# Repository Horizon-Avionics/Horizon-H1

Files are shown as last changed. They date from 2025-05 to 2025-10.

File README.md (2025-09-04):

# Horizon Avionics

## Building a fully open-source flight computer.

### Hardware By @Scooter Y, and @Meddy B.
### Software By: @Stars, and @Chocowafer

------

#### About:

The Goal of Horizon Avionics is to be able to build a full-fledged, and open-source flight computer for amateur rocketry. There is no such board online, and we are hoping for this board to streamline open-sourcing products instead of charging upwards of $400 for a ~$130 board.

#### Features:

- This whole board including antennas are under $150 USD.

- IMU/Baro for our sensor data.

- GPS for navigation of where the rocket landed and it's flight path.

- RF - Including a transmit tower for receiving/sending data from the rocket live during the flight.

- NAND + Micro SD Card Storage for logging.

- 3 MCU's each controlling different ascpetcs of the flight computer- MMCU, TMCU, NMCU.

- H-Bridge for servo movement.

- Working PWM for TVC and/or Reaction Wheel

- Pyro-channels for parachute deployment

  ------

#### How it's all gonna work:

For the most part, this will all be explained over on the software repo, but a short synopsis will be provided below.

In short, we have 3 micro-controllers, the MMCU, the TMCU, and the NMCU. Each one of these MCU's is responsible for a different aspect of the functionality of the flight computer.  

- **The TMCU**

	The TMCU is responsible for a number of different things. It takes in all the raw data from the IMU, Baro and the GPS data and sending it to the MMCU via SPI for filtering and logging. It is also resposible for sending and receiving the radio packets. In-short, the TMCU does a lot of different things for this board to make room for the MMCU to do the heavy lifting.

- **The NMCU**

  The NMCU is responsible for more of the physical actions of the rocket. It's main jobs are to on boot, load the saved state, for position movements, and while in-flight, it's jobs are to take in the filtered data from the MMCU, and use it to control the Camera, servo lines, reaction wheel, and pyro-channels.

- **The MMCU**

  The MMCU is our main MCU. It's main responsibilities are to, while in flight, take in all the data from the TMCU, put it through a filter (we will be using the Kalman Filter for our board as it is the best one we have found to remove noise and such), package the data, and send it back off to the TMCU for radio sending or to the NMCU for movments. Along with sending it to the nessecary MCU's, it also sends the packaged, and filtered data to the NAND which will eventually be moved to the SD Card + the Camera footage upon landing.

------

#### Getting Started

To view the different changes between commits, check it out over on [CADLAB.io](https://cadlab.io/project/29344).

##### Checkout locally

1. `git clone https://github.com/Horizon-Avionics/Horizon-Avionics-Hardware`

2. Open the corresponding folder in KiCad 9.0

### Some Photos So Far







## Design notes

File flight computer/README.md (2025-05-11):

# Horizon Avionics

## Building a fully open-source flight computer. Built by Hack Clubbers For Hack Clubbers

### By @Scooter Y, @Stars, @Meddy B, @YourLocalDndNerd

------

#### About:

The Goal of Horizon Avionics was to be able to build a full-fledged, and open-source flight computer for amateur rocketry. There is no such board online, and we are hoping for this board to streamline open-sourcing products instead of charging upwards of $400 for a ~$100 board.

#### Goals:

- Keep this board under $150 USD

- IMU/Baro

- GPS

- RF - Including a transmit tower for receiving/sending data from the rocket

- NAND + Micro SD Card Storage for logging

- 3 MCU's - MMCU, TMCU, NMCU

- H-Bridge

- Working PWM for TVC and/or Reaction Wheel

  ------

#### How it's all gonna work:

For the most part, this will all be explained over on the software repo, but a short synopsis will be provided below.

In short, we have 3 micro-controllers, the MMCU, the TMCU, and the NMCU. Each one of these MCU's is responsible for a different aspect of the functionality of the flight computer.  

- **The TMCU**

	The TMCU is responsible for a number of different things. It takes in all the raw data from the IMU, Baro and the GPS data and sending it to the MMCU via SPI for filtering and logging. 

- **The NMCU**

- **The MMCU**

------

#### Getting Started

To view the diff changes between commits, check it out over on [CADLAB.io](https://cadlab.io/project/29344).

##### Checkout locally

1. `git clone https://github.com/Horizon-Avionics/Horizon-Avionics-Hardware`

2. Open the corresponding folder in KiCad 9.0

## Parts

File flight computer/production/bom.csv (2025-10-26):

Designator | Footprint | Quantity | Value | LCSC Part #
1X3SERVO1 | PinHeader_1x03_P2.54mm_Vertical | 1 | Conn_01x03
BZ2 | MLT-8530_JHE | 1 | Buzzer
C1, C2 | 0603 | 2 | 100 nF
C10, C17 | 0603 | 2 | 12pF
C11, C13, C15, C19, C44, C45, C5, C50, C51, C6, C7, C77, C8, C9 | 0603 | 14 | 100nF
C12, C22, C35, C63, C72 | 0603 | 5 | 1uF
C16 | 0603 | 1 | 4n7
C18, C67 | 0603 | 2 | 4.7uF
C20, C23, R1 | 0603 | 3 | DNP
C21, C24, C25, C28, C32 | 0603 | 5 | 10uF
C26 | 0603 | 1 | 100pF
C27 | 0603 | 1 | 100n
C33 | 0603 | 1 | 3.3 nF
C34 | 0603 | 1 | 22uF
C36 | 0603 | 1 | 1u
C37, C38 | 0603 | 2 | 100nF | C14663
C4 | 0603 | 1 | 1.2 pF
C40 | 0603 | 1 | 470nF | C1623
C46 | 0603 | 1 | 1nF | C100040
C47 | 0603 | 1 | 47nF | C107093
C48 | 0603 | 1 | 47pF | C105622
C49 | 0603 | 1 | 100pF | C14665
C64, C65, C66 | 0603 | 3 | 0.1uF
D1 | 0603 | 1 | D_Schottky
D15, D16, D17, D18 | LED_ROHM_SMLVN6 | 4 | SMLVN6RGB
D20, D26 | Nexperia_CFP3_SOD-123W | 2 | PMEG6020ER
D21, D22, D3, D4, D7 | 0603 | 5 | LED
D8 | SOT-143 | 1 | PRTR5V0U2X
F1, F2 | 0603 | 2 | Polyfuse
FB1 | 0603 | 1 | BLM18AG601SN1D
J1 | microSD_HC_Hirose_DM3D-SF | 1 | Micro_SD_Card_Det1
J10 | TerminalBlock_Phoenix_MPT-0,5-2-2.54_1x02_P2.54mm_Horizontal | 1 | Conn_01x02_Pin
J11 | USB_C_Receptacle_GCT_USB4105-xx-A_16P_TopMnt_Horizontal | 1 | USB_C_Receptacle_USB2.0_16P
J12 | PinHeader_1x04_P2.54mm_Vertical | 1 | Conn_01x04
J13, J14, J6, J9 | PinHeader_1x03_P2.54mm_Vertical | 4 | 1x3 servo
J15, J16 | TerminalBlock_Phoenix_MPT-0,5-2-2.54_1x02_P2.54mm_Horizontal | 2 | arming terminal
J17, J3, J4 | U.FL_Hirose_U.FL-R-SMT-1_Vertical | 3 | H9161TR-ND
J18, J2, J21, J7, J8 | PinHeader_2x03_P2.54mm_Vertical | 5 | Conn_02x03_Counter_Clockwise
J19, J20 | TerminalBlock_Phoenix_MPT-0,5-2-2.54_1x02_P2.54mm_Horizontal | 2 | Screw_Terminal_01x02
J22 | PinHeader_2x03_P2.54mm_Vertical | 1 | Bluetooth Programming
J5 | TerminalBlock_Phoenix_MPT-0,5-2-2.54_1x02_P2.54mm_Horizontal | 1 | Screw_Term
L10 | 0603 | 1 | 47nH | C285885
L11 | 0805 | 1 | 15uH | C383402
L2 | L_APV_ANR4018 | 1 | 2.2uH
L3 | 0603 | 1 | 3.9 nH
Q2 | SOT-23 | 1 | DMG2301L
Q7 | SOT-23 | 1 | BSS138
Q8, Q9 | SOT-23 | 2 | IRLML6402
R10, R13, R26, R29, R30 | 0603 | 5 | 2.2k
R11, R12, R54, R55 | 0603 | 4 | 10kΩ
R14, R9 | 0603 | 2 | 1.5k
R2 | 0603 | 1 | 0R
R20, R21 | 0603 | 2 | 5k1
R22, R47 | 0603 | 2 | 330
R27, R3, R38, R39, R4, R5, R52, R53, R56, R78, R80 | 0603 | 11 | 10k
R42 | 1206 | 1 | 900k
R43, R45 | 0603 | 2 | 100k
R44 | 0603 | 1 | 350k
R46, R79, R81 | 0603 | 3 | 100
R58, R59 | 0603 | 2 | 1k
R6, R7 | 0603 | 2 | 4.7k
R72 | 0603 | 1 | 2k2
R8 | 0603 | 1 | 100 | C105588
R87, R88, R89, R90, R91, R92, R93, R94, R95, R96, R97, R98 | 0603 | 12 | 220
SAMD21G18A-AU1 | TQFP-48_7x7mm_P0.5mm | 1 | NMCU
SAMD21G18A-AU2 | TQFP-48_7x7mm_P0.5mm | 1 | TMCU
SW1 | SW_SPST_CK_KMS2xxGP | 1 | CK_KMS2xxG
U1 | QFP50P1200X1200X160-64N | 1 | MMCU
U10 | LGA-14_3x2.5mm_P0.5mm_LayoutBorder3x4y | 1 | LSM6DS3
U11 | BGM220S_SIL | 1 | BGM220SC12WGA2R
U13 | TSOT-23-6 | 1 | LTC4412xS6
U15 | SOT-23-5 | 1 | AP2112K-3.3
U16 | QFN-24-1EP_4x4mm_P0.5mm_EP2.6x2.6mm | 1 | SX1262IMLTRT | C191341
U17 | SOT-363_SC-70-6 | 1 | PE4259 | C470892
U2 | QFN-16-1EP_3x3mm_P0.5mm_EP1.9x1.9mm | 1 | MKL02Z32VFG4
U3 | Texas_S-PVSON-N10_ThermalVias | 1 | TPS61200DRC
U5 | ST_HLGA-10_2x2mm_P0.5mm_LayoutBorder3x2y | 1 | LPS22HB
U6 | Quectel_L96 | 1 | GPS
U8 | SOIC-8_5.3x5.3mm_P1.27mm | 1 | NAND
U9 | Texas_SIL0008D_MicroSiP-8-1EP_2.8x3mm_P0.65mm_EP1.1x1.9mm_ThermalVias | 1 | TPS82130
Y1 | Crystal_SMD_3215-2Pin_3.2x1.5mm | 1 | 32 kHZ
Y2 | Crystal_SMD_3225-4Pin_3.2x2.5mm | 1 | 32MHz | C37635386

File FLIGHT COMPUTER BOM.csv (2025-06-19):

Manufacturer Part Number | Quantity | Digi-Key Part Number | Total Price | Customer Reference
MK20DX256VLH7 | 1 | MK20DX256VLH7-ND | $11.94
W25Q128JVSIQ | 1 | W25Q128JVSIQ-ND | $2.39
A3909GLNTR-T | 1 | 620-1498-1-ND | $1.92
BGM220SC12WGA2R | 1 | 336-BGM220SC12WGA2RCT-ND | $10.37
TPS61092RSAR | 1 | 296-15240-1-ND | $3.46
LTC4412IS6#TRMPBF | 1 | 505-LTC4412IS6#TRMPBFCT-ND | $9.78
TB006-508-02BE | 5 | 102-6191-ND | $3.80
61301011121 | 5 | 732-2670-ND | $6.25
AP2112K-3.3TRG1 | 1 | AP2112K-3.3TRG1DICT-ND | $0.34
PRTR5V0U2X,215 | 3 | 1727-3884-1-ND | $2.04
AT-0927-TT-6-R | 1 | 668-1462-ND | $1.53
BSS138 | 1 | BSS138CT-ND | $0.41
DM3D-SF | 1 | HR1941CT-ND | $2.46
SMLVN6RGB1W1 | 3 | 846-1187-1-ND | $6.69
ABS07-32.768KHZ-7-T | 2 | 535-9543-1-ND | $2.54
W1030 | 2 | 553-1309-ND | $11.60
1052620001 | 1 | WM9669-ND | $3.07
LG Q396-PS-35-0-20-R18 | 10 | 475-LGQ396-PS-35CT-ND | $1.86
PMEG6020ER,115 | 5 | 1727-5217-1-ND | $2.85 | D19, D20, D23, D26
0603L010YR | 3 | F2900CT-ND | $4.44
GRM022R60J104ME15L | 10 | 490-7192-1-ND | $0.36
CRGCQ0603J220R | 10 | A130087CT-ND | $0.36
RC0603FR-074K7L | 2 | 311-4.70KHRCT-ND | $0.32
RC0603FR-07430KL | 1 | 311-430KHRCT-ND | $0.16
RC0603FR-07100KL | 20 | 311-100KHRCT-ND | $0.28
RC0603FR-075K1L | 10 | 311-5.10KHRCT-ND | $0.14
RMCF0603JT10K0 | 50 | RMCF0603JT10K0CT-ND | $0.82
RC0201FR-0733RL | 10 | 311-33.0MCT-ND | $0.17
RC0201FR-071KL | 10 | 311-1KMCT-ND | $0.14
RC0603FR-072K2L | 2 | 311-2.20KHRCT-ND | $0.32
IRLML6402TRPBF | 10 | IRLML6402PBFCT-ND | $3.26
DMG2301L-7 | 1 | DMG2301L-7DICT-ND | $0.36
PPTC032LFBN-RC | 3 | S7071-ND | $2.10
61300411821 | 1 | 732-61300411821-ND | $0.58
NSR01L30MXT5G | 1 | NSR01L30MXT5GOSCT-ND | $0.26 | D1
TMK107ABJ225KA-T | 1 | 587-2909-1-ND | $0.12
CL10A226MP8NUNE | 1 | 1276-1274-1-ND | $0.12
CL10B105KP8NNNC | 10 | 1276-1946-1-ND | $0.07
GRM0335C1H1R2CA01D | 2 | 490-6119-1-ND | $0.30
C0603C332K4REC7411 | 1 | 399-C0603C332K4REC7411CT-ND | $0.15
C0603C220J5GACTU | 2 | 399-C0603C220J5GACTUCT-ND | $0.34
CL10A106KQ8NNNC | 3 | 1276-1038-1-ND | $0.36
C0603C103M4REC7411 | 10 | 399-C0603C103M4REC7411CT-ND | $0.79
C0603X102K5RAC3316 | 2 | 399-C0603X102K5RAC3316CT-ND | $1.02
CL10A475KP8NNNC | 2 | 1276-1044-1-ND | $0.24
C0603C472K4RECAUTO | 3 | 399-17879-1-ND | $0.57
CBR02C120F3GAC | 2 | 399-8604-1-ND | $1.10
B82496C3470J000 | 1 | 495-1838-1-ND | $0.41
LRC0201BS3N9GV001T | 2 | 712-LRC0201BS3N9GV001TCT-ND | $0.30
RC0603FR-13330KL | 2 | 13-RC0603FR-13330KLCT-ND | $0.32 | 330 instead of 350K
PESD5V0S1UL,315 | 1 | 1727-4189-1-ND | $0.19 | D2
CONMHF1-SMD-T | 1 | 343-CONMHF1-SMD-TCT-ND | $0.29
124019772112A | 1 | 664-124019772112ACT-ND | $2.73
0733910070 | 2 | WM5544-ND | $10.94
ATSAMD21G18A-AU | 2 | ATSAMD21G18A-AU-ND | $12.90
CC0603KRX5R8BB104 | 38 | 13-CC0603KRX5R8BB104CT-ND | $1.94
GRM0335C1H2R7CA01D | 2 | 490-11323-1-ND | $0.30
GRM0335C1H2R2CA01D | 10 | 490-6125-1-ND | $0.20
C0603X104M5RACTU | 1 | 399-C0603X104M5RACTUCT-ND | $0.60
GRM0335C1H1R8CA01D | 2 | 490-11314-1-ND | $0.30
GJM0335C1E1R0WB01D | 2 | 490-10677-1-ND | $0.32
GJM0335C1E1R5BB01D | 2 | 490-11175-1-ND | $0.30
XL2ED8K5OI-111YXC-32M | 2 | 4029-XL2ED8K5OI-111YXC-32MCT-ND | $1.00
0734120114 | 1 | WM3894CT-ND | $1.28
LQM18DN6R8M70L | 1 | 490-LQM18DN6R8M70LCT-ND | $0.17
LSM6DSO32TR | 1 | 497-LSM6DSO32CT-ND | $5.66
ERJ-1GNF1000C | 10 | P122654CT-ND | $0.60
LQG18HN6N8J00D | 2 | 490-1108-1-ND | $0.40
LQP03TN8N2H02D | 2 | 490-6740-1-ND | $0.30
L96-M33 | 1 | 2958-L96-M33CT-ND | $20.64
C470892 | 3 |  | $1.86
C94049 | 3 |  | $2.30
C163210 | 3 |  | $5.25
C3013581 | 100 |  | $0.81
C90205 | 100 |  | $0.58
SW1, SW2
TP1, TP2
R26, R29, R30
TOTAL BEFORE TAX + SHIPPING |  |  | $177.44USD

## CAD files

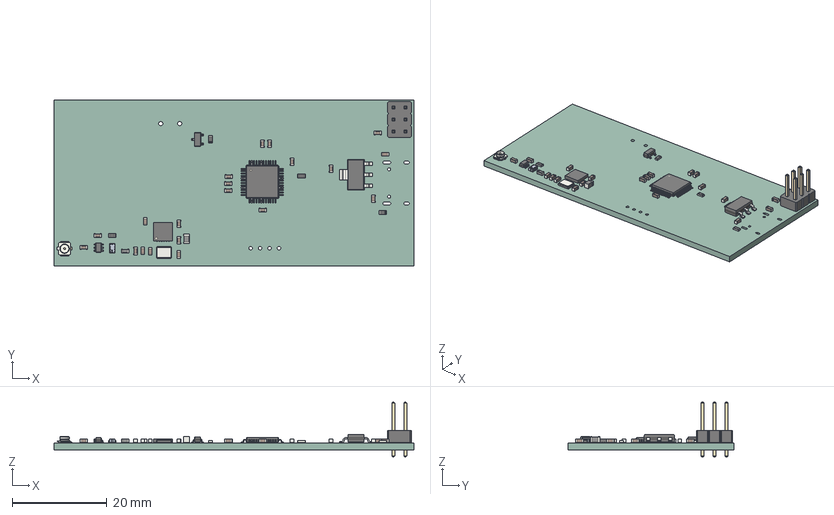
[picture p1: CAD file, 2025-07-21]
ground station/gs.step
76.0 x 35.0 x 11.5 mm
C_0603_1608Metric x 20
R_0603_1608Metric x 4
L_0603_1608Metric
SOT-23
Crystal_SMD_3225-4Pin_3.2x2.5mm
U.FL_Hirose_U.FL-R-SMT-1_Vertical
SOT-363_SC-70-6
SOT-223
QFN-24-1EP_4x4mm_P0.5mm_EP2.6x2.6mm
gs 1.27.1
gs 1.27.2
gs 1.27.3
PinHeader_2x03_P2.54mm_Vertical
TQFP-48_7x7mm_P0.5mm
L_0805_2012Metric
gs_PCB

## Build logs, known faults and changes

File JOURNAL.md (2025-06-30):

Day 1- Friday \- \~4 hours:

- Came up with the idea of building a fully open-source flight computer for amateur rocketry.  
- Started to put together a team, and started researching parts to use  
- Came up with a rough-plan on what we want out of this and our parts selection (On Tab 1 on all the charts)

Day 2- Saturday \- \~3 Hours:

- Finalized parts selections  
- Started work on software

Day 3 \- sunday \- \~7.5

- discussed potential solutions in order to program all 3 chips with 1 usb-c connector  
- looked into alternatives, and what other people have done  
- looked into additional sensors/regulators that we will use  
- Continued to work on software- developed most of the code for the IMU’s, GPS and stuff.

Day 4 \- monday \- \~4 hours:

- Figuring out a big bug in the code and  
- final solution for programming   
- working on solution for data/power, and allowing us to flash 3 MCU’s with only one USB-C connector

Day 5 \- tuesday \- \~6.5 hours (3.5 hours huddle, 2 hours Meddy by himself afterwards, and 1 hour just Liam for software):

- Finished the switch multiplexer stuff.  
- Finished the solution for data/power, and allowing us to flash 3 MCU’s with only one USB-C connector  
- Changed a few small power rail stuff

Day 6 \- Wednesday \- \~4 hours:

- Built the full schematics for the IMU via SPI to the TMCU/

Day 7 \- Thursday \- \~4.5 hours from @Scooter Y, 4 hours from @Meddy B:

- Finally finished building the GPS module  
  - Had to figure out how to wire up the antenna, and which one to use (which ended up being the LNA one…)  

- Finished wiring up the radio tuned at 915 MHZ to bypass HAM restrictions including all the SPI magic and the antennas for it  
  
- Built the schematic for the H-Bridge which is responsible for controlling the servos for the reaction wheel  

- Fixed some net flag issues where I forgot to wire it to the MCU…

Day 9- Saturday- \~8 hours from @Scooter Y, @Meddy B, and @Stars:

- Added Bluetooth to the Schematic for making changes to the codebase and flashing it to the MCU’s wirelessly (especially useful on the launch pad for last minute changes). A big   
  Trouble was trying to figure out how to get it to 2.3GHZ. I had to calc π-type to figure out what to use to get it to the right frequency.  



- 

Day 10 \- sunday the 18th \~15 hours from @meddy and @scooter y (We worked from like 1am to 4am\!)

- Today was a big day for us. We started off with doing some schematic work and adding a lot of the needed footprints like for BL. After that, we did the layout for pcb and wired up sensors and putting it on the pcb, although U didnt finish wiring everything to the power rails and mcu. I (@scooter) started the routing too for the bl chip, along with the cs, sck for rf chip as that takes time since it is a very sensitive ic. ill finish after i sleep. i need to fix the jtag/swd connectors as well.





Day 11 \- Thursday \- May 22nd \- 4 hours

- started redoing layout

Day 12 \- Friday \- May 23rd \- 13 hours

- Started wiring, got stuck and realized the layout was bad so I scrapped it and did it again so I started a new layout. We didn’t have enough space on the PCB to properly route all the sensitive components. Also, idk what we were on, but we also had WAY too many screw terminals, we should only have like 5, not 12\.

Day 13 \- saturday \- May 24th \- 2 hours

- I realized the layout was bad so I did it one more time. Started it- not finished it ;)

Day 14 \- sunday \- May 25th \- 5 hours

- redid layout, starting wiring some more, and this time, it finally seems to be a lot nicer




Through every revision it looks very similar because we have an idea of what we want with the end result, but the process of laying out every single part and the specific wiring seems to change so its not really the same every time. For example for this revision, we have the screw terminals on the top to allow more space on the sides for ant’s and stuff.

Day 15 \- May 26th \- 3 hours (@Meddy)

- Don’t really remember what I exactly wired up on this day :pf:, but I did some PCB routing, most likely regarding the MCU routing.

Day 16 \- May 27th \- 4 hours

- Did some more routing on this day- nothing crazy. I mostly re-arranged this github repo’s folders since it was a mess\!

Ive worked on it at random misc times and forgot to record  
Day 17(latest day ive acc recorded) 6/1 13 hours

- I completely redid the entire layout. Our first approach was laying everything out and then wiring, whereas with my latest version, I was focused on completing entire parts. Like completely wiring everything for a sensor, before wiring up the next part. I think this approach helped cuz now everything is actually able to fit(except the bootloader pins). The good thing is even though it was a full re-wiring, the layout was kept very similar, and it was more the way I routed it over the parts placement.  

- finished complete wiring, still need bootloader pins. worst case scenario ill will the wires directly to the mcu  



Day 18 \- June 2nd \- 5 hours:

- literally just random wiring

Day 19 \- June 3rd \- 6 hours:

- Finished the layout placement ie. all the parts are now all placed now, and just the few left need to be routed, and all the MCU routing. 

Day 20 \- June 4th \- 4 hours:

- Fixes over 200 DRC errors. Now I only have 84 errors left (yay, I guess).... I also wired up the bootloader pins which will be able to be broken off once programmed for the first time. I routed this with Meddy.

Day 21 \- June 5th: maybe 3 hours?

- finally a day without wiring. fixed all drc errors. I started working on the warnings, and then I realized that I could ignore them since they were all about the silkscreens. Instead I only needed to fix the actual errors. I did that. A lot of traces didn't have space between each other since everything is so tightly packed. I cleaned up random misc traces and stuff. Everything should pretty much be good now.

Day 22 \- June 6th: 3 hours:

- So apparently even though we thought there were no DRC errors left, there somehow were :(. For some reason each device said more so we fixed those (which were actual DRC errors, I'm confused.) Nonetheless, we fixed most of the DRC errors.

Day 23 \- June 13th: 3 hours:

- Tided everything up, and finally finished all the hole DRC’s \+ trace spacing DRC’s\!

Day 24 \- 4 hours:

- I fixed the ground pour to be all 4 layers over just the top and bottom since it would be better. I also switched out the BL, and GPS antenna’s to U.FL since apparently SMA antennas for these don’t exist.. I also did some ground stitching around the GPS, BL, and RF since those need to have ground stitching and I didn’t add it yet.

Day 25 \- June 18th \- 10 minutes:

- Added the PCBWAY logo to our board since they will be sponsoring the PCB it seems like.

All of @yourlocaldndnerd's time \- 13 hours programming + \~30 hours of docs and design
- I keep forgetting to add any of my time, so this is all of mine combined into one slot.
- I mostly just programmed the gps, radio (which were completed by around day 15), and the kalman filters (still needs testing)

**Total hours worked on it so far- \~128.6 hours**  
**Links-**   
[**https://github.com/Horizon-Avionics/Horizon-Avionics-Hardware**](https://github.com/Horizon-Avionics/Horizon-Avionics-Hardware)  
[**https://github.com/Horizon-Avionics/Horizon-Avionics-Software**](https://github.com/Horizon-Avionics/Horizon-Avionics-Software)

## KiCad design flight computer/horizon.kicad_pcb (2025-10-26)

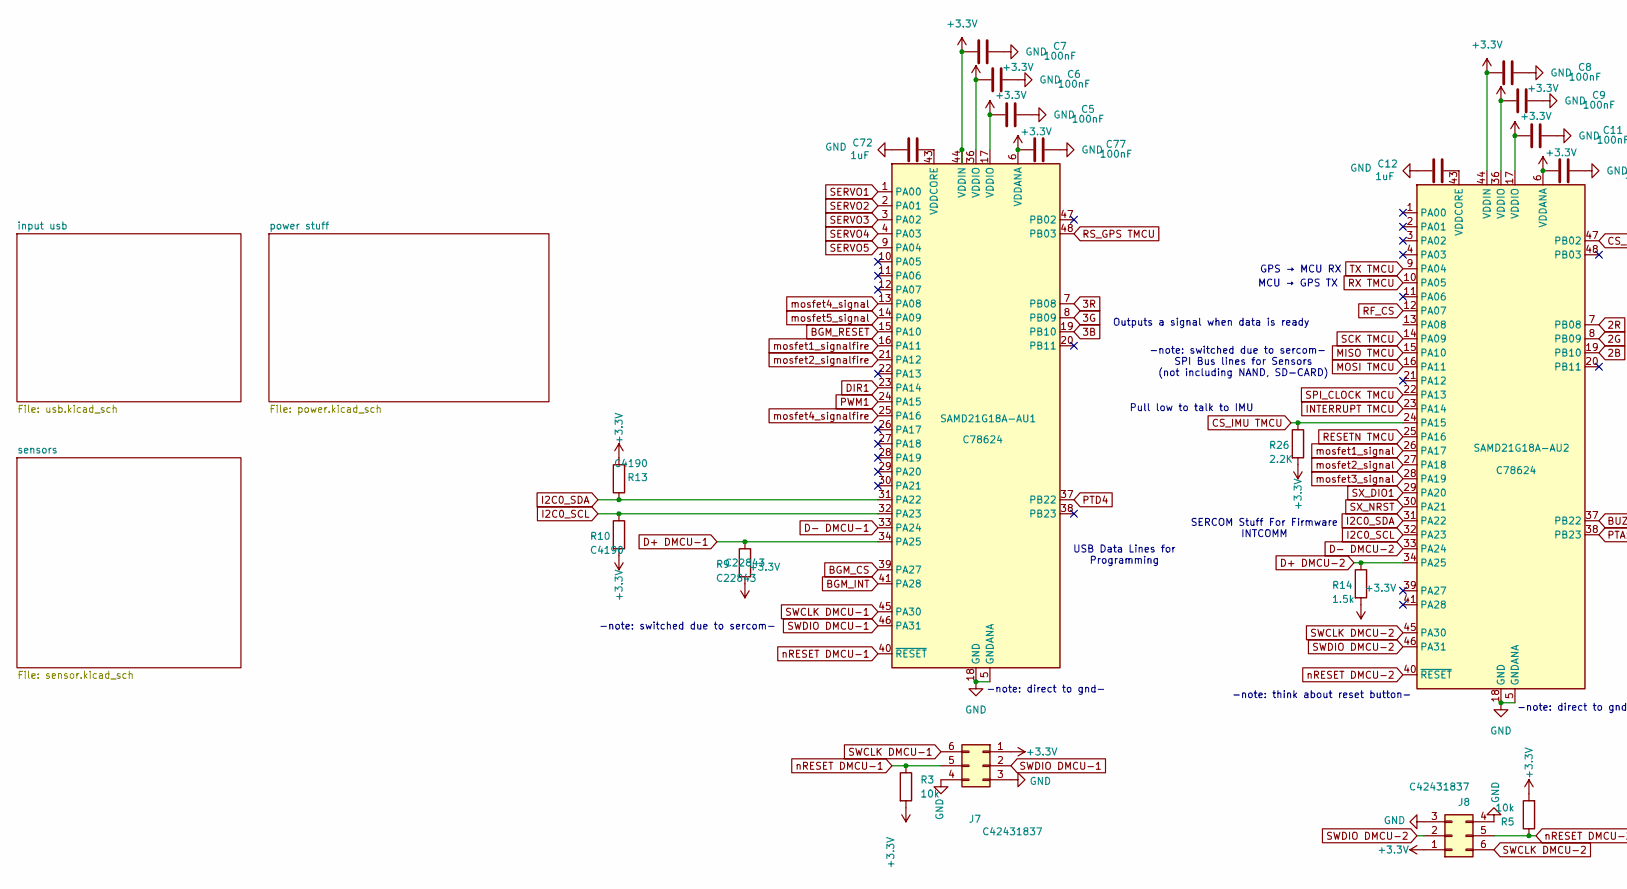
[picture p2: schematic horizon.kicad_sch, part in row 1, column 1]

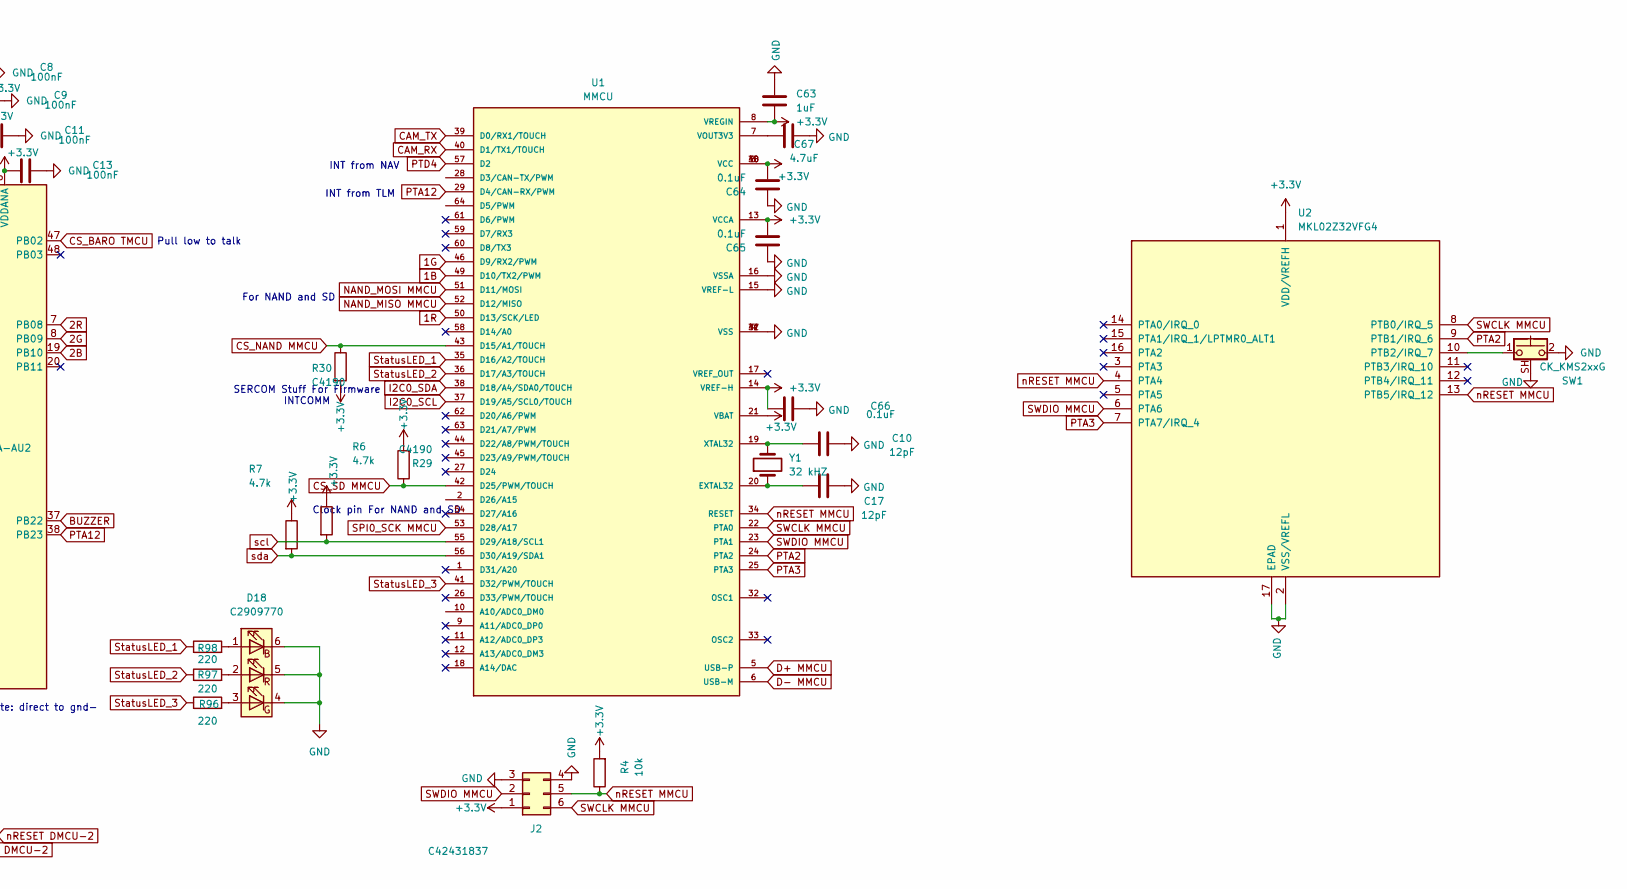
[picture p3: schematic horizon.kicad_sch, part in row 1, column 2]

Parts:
C5, C6, C7, C8, C9, C11, C13, C77: 100nF; C_0603_1608Metric
C10, C17: 12pF; C_0603_1608Metric
C12, C63, C72: 1uF; C_0603_1608Metric
C64, C65, C66: 0.1uF; C_0603_1608Metric
C67: 4.7uF; C_0603_1608Metric
D18: C2909770; LED_ROHM_SMLVN6
J2, J7, J8: C42431837; PinHeader_2x03_P2.54mm_Vertical
R3, R4, R5: 10k; R_0603_1608Metric
R6, R7: 4.7k; R_0603_1608Metric
R9: C22843; R_0603_1608Metric; LCSC C22843
R10, R13, R29, R30: C4190; R_0603_1608Metric
R14: 1.5k; R_0603_1608Metric
R26: 2.2K; R_0603_1608Metric
R96, R97, R98: 220; R_0603_1608Metric
SAMD21G18A-AU1, SAMD21G18A-AU2: C78624; TQFP-48_7x7mm_P0.5mm
SW1: CK_KMS2xxG; SW_SPST_CK_KMS2xxGP
U1: MMCU; QFP50P1200X1200X160-64N
U2: MKL02Z32VFG4; QFN-16-1EP_3x3mm_P0.5mm_EP1.9x1.9mm
Y1: 32 kHZ; Crystal_AT310_D3.0mm_L10.0mm_Vertical

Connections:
1B: U1.49 (D10/TX2/PWM); also elsewhere on the board
1G: U1.46 (D9/RX2/PWM); also elsewhere on the board
1R: U1.50 (D13/SCK/LED); also elsewhere on the board
2B: SAMD21G18A-AU2.19 (PB10); also elsewhere on the board
2G: SAMD21G18A-AU2.8 (PB09); also elsewhere on the board
2R: SAMD21G18A-AU2.7 (PB08); also elsewhere on the board
3B: SAMD21G18A-AU1.19 (PB10); also elsewhere on the board
3G: SAMD21G18A-AU1.8 (PB09); also elsewhere on the board
3R: SAMD21G18A-AU1.7 (PB08); also elsewhere on the board
+3.3V: C5.2, C6.2, C7.2, C8.2, C9.2, C11.2, C13.2, C63.1, C64.1, C65.1, C66.1, C77.2, J2.1, J7.1, J8.1, R3.2, R4.2, R5.2, R6.1, R7.1, R9.2, R10.2, R13.2, R14.2, R26.2, R29.2, R30.2, SAMD21G18A-AU1.6 (VDDANA), SAMD21G18A-AU1.17 (VDDIO), SAMD21G18A-AU1.36 (VDDIO), SAMD21G18A-AU1.44 (VDDIN), SAMD21G18A-AU2.6 (VDDANA), SAMD21G18A-AU2.17 (VDDIO), SAMD21G18A-AU2.36 (VDDIO), SAMD21G18A-AU2.44 (VDDIN), U1.3 (VCC), U1.8 (VREGIN), U1.13 (VCCA), U1.14 (VREF-H), U1.21 (VBAT), U1.30 (VCC), U1.48 (VCC), U2.1 (VDD/VREFH); also elsewhere on the board
BGM_CS: SAMD21G18A-AU1.39 (PA27); also elsewhere on the board
BGM_INT: SAMD21G18A-AU1.41 (PA28); also elsewhere on the board
BGM_RESET: SAMD21G18A-AU1.15 (PA10); also elsewhere on the board
BUZZER: SAMD21G18A-AU2.37 (PB22); also elsewhere on the board
CAM_RX: U1.40 (D1/TX1/TOUCH); also elsewhere on the board
CAM_TX: U1.39 (D0/RX1/TOUCH); also elsewhere on the board
CS_BARO TMCU: SAMD21G18A-AU2.47 (PB02); also elsewhere on the board
CS_IMU TMCU: R26.1, SAMD21G18A-AU2.24 (PA15); also elsewhere on the board
CS_NAND MMCU: R30.1, U1.43 (D15/A1/TOUCH); also elsewhere on the board
CS_SD MMCU: R29.1, U1.42 (D25/PWM/TOUCH); also elsewhere on the board
D+ DMCU-1: R9.1, SAMD21G18A-AU1.34 (PA25); also elsewhere on the board
D+ DMCU-2: R14.1, SAMD21G18A-AU2.34 (PA25); also elsewhere on the board
D+ MMCU: U1.5 (USB-P); also elsewhere on the board
D- DMCU-1: SAMD21G18A-AU1.33 (PA24); also elsewhere on the board
D- DMCU-2: SAMD21G18A-AU2.33 (PA24); also elsewhere on the board
D- MMCU: U1.6 (USB-M); also elsewhere on the board
DIR1: SAMD21G18A-AU1.23 (PA14)
GND: C5.1, C6.1, C7.1, C8.1, C9.1, C10.2, C11.1, C12.1, C13.1, C17.2, C63.2, C64.2, C65.2, C66.2, C67.2, C72.1, C77.1, D18.4 (GK), D18.5 (RK), D18.6 (BK), J2.3, J2.4, J7.3, J7.4, J8.3, J8.4, SAMD21G18A-AU1.5 (GNDANA), SAMD21G18A-AU1.18 (GND), SAMD21G18A-AU1.35 (GND), SAMD21G18A-AU1.42 (GND), SAMD21G18A-AU2.5 (GNDANA), SAMD21G18A-AU2.18 (GND), SAMD21G18A-AU2.35 (GND), SAMD21G18A-AU2.42 (GND), SW1.2, SW1.SH (B), U1.4 (VSS), U1.15 (VREF-L), U1.16 (VSSA), U1.31 (VSS), U1.47 (VSS), U2.2 (VSS/VREFL), U2.17 (EPAD); also elsewhere on the board
I2C0_SCL: R10.1, SAMD21G18A-AU1.32 (PA23), SAMD21G18A-AU2.32 (PA23), U1.37 (D19/A5/SCL0/TOUCH); also elsewhere on the board
I2C0_SDA: R13.1, SAMD21G18A-AU1.31 (PA22), SAMD21G18A-AU2.31 (PA22), U1.38 (D18/A4/SDA0/TOUCH); also elsewhere on the board
INTERRUPT TMCU: SAMD21G18A-AU2.23 (PA14); also elsewhere on the board
MISO TMCU: SAMD21G18A-AU2.15 (PA10); also elsewhere on the board
MOSI TMCU: SAMD21G18A-AU2.16 (PA11); also elsewhere on the board
NAND_MISO MMCU: U1.52 (D12/MISO); also elsewhere on the board
NAND_MOSI MMCU: U1.51 (D11/MOSI); also elsewhere on the board
unnamed: D18.1 (BA), R98.2
unnamed: D18.3 (GA), R96.2
unnamed: D18.2 (RA), R97.2
unnamed: C72.2, SAMD21G18A-AU1.43 (VDDCORE)
unnamed: C12.2, SAMD21G18A-AU2.43 (VDDCORE)
unnamed: C17.1, U1.20 (EXTAL32), Y1.1
unnamed: C67.1, U1.7 (VOUT3V3)
unnamed: C10.1, U1.19 (XTAL32), Y1.2
unnamed: SW1.1, U2.10 (PTB2/IRQ_7)
PTA2: U1.24 (PTA2), U2.9 (PTB1/IRQ_6)
PTA3: U1.25 (PTA3), U2.7 (PTA7/IRQ_4)
PTA12: SAMD21G18A-AU2.38 (PB23), U1.29 (D4/CAN-RX/PWM)
PTD4: SAMD21G18A-AU1.37 (PB22), U1.57 (D2)
PWM1: SAMD21G18A-AU1.24 (PA15)
RESETN TMCU: SAMD21G18A-AU2.25 (PA16)
RF_CS: SAMD21G18A-AU2.12 (PA07); also elsewhere on the board
RS_GPS TMCU: SAMD21G18A-AU1.48 (PB03); also elsewhere on the board
RX TMCU: SAMD21G18A-AU2.10 (PA05); also elsewhere on the board
SCK TMCU: SAMD21G18A-AU2.14 (PA09); also elsewhere on the board
SERVO1: SAMD21G18A-AU1.1 (PA00); also elsewhere on the board
SERVO2: SAMD21G18A-AU1.2 (PA01); also elsewhere on the board
SERVO3: SAMD21G18A-AU1.3 (PA02); also elsewhere on the board
SERVO4: SAMD21G18A-AU1.4 (PA03); also elsewhere on the board
SERVO5: SAMD21G18A-AU1.9 (PA04); also elsewhere on the board
SPI0_SCK MMCU: U1.53 (D28/A17); also elsewhere on the board
SPI_CLOCK TMCU: SAMD21G18A-AU2.22 (PA13); also elsewhere on the board
SWCLK DMCU-1: J7.6, SAMD21G18A-AU1.45 (PA30)
SWCLK DMCU-2: J8.6, SAMD21G18A-AU2.45 (PA30)
SWCLK MMCU: J2.6, U1.22 (PTA0), U2.8 (PTB0/IRQ_5)
SWDIO DMCU-1: J7.2, SAMD21G18A-AU1.46 (PA31)
SWDIO DMCU-2: J8.2, SAMD21G18A-AU2.46 (PA31)
SWDIO MMCU: J2.2, U1.23 (PTA1), U2.6 (PTA6)
SX_DIO1: SAMD21G18A-AU2.29 (PA20); also elsewhere on the board
SX_NRST: SAMD21G18A-AU2.30 (PA21); also elsewhere on the board
StatusLED_1: R98.1, U1.35 (D16/A2/TOUCH)
StatusLED_2: R97.1, U1.36 (D17/A3/TOUCH)
StatusLED_3: R96.1, U1.41 (D32/PWM/TOUCH)
TX TMCU: SAMD21G18A-AU2.9 (PA04); also elsewhere on the board
mosfet1_signal: SAMD21G18A-AU2.26 (PA17)
mosfet1_signalfire: SAMD21G18A-AU1.16 (PA11); also elsewhere on the board
mosfet2_signal: SAMD21G18A-AU2.27 (PA18)
mosfet2_signalfire: SAMD21G18A-AU1.21 (PA12); also elsewhere on the board
mosfet3_signal: SAMD21G18A-AU2.28 (PA19)
mosfet4_signal: SAMD21G18A-AU1.13 (PA08)
mosfet4_signalfire: SAMD21G18A-AU1.25 (PA16)
mosfet5_signal: SAMD21G18A-AU1.14 (PA09)
nRESET DMCU-1: J7.5, R3.1, SAMD21G18A-AU1.40 (~RESET)
nRESET DMCU-2: J8.5, R5.1, SAMD21G18A-AU2.40 (~RESET)
nRESET MMCU: J2.5, R4.1, U1.34 (RESET), U2.4 (PTA4), U2.13 (PTB5/IRQ_12)
scl: R6.2, U1.55 (D29/A18/SCL1)
sda: R7.2, U1.56 (D30/A19/SDA1)

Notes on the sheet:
SERCOM Stuff For Firmware INTCOMM
-note: direct to gnd-
For NAND and SD
-note: switched due to sercom-
Pull low to talk to IMU
INT from TLM
Pull low to talk
GPS → MCU RX
Clock pin For NAND and SD
MCU → GPS TX
Outputs a signal when data is ready
-note: think about reset button-
INT from NAV
USB Data Lines for Programming
SPI Bus lines for Sensors (not including NAND, SD-CARD)

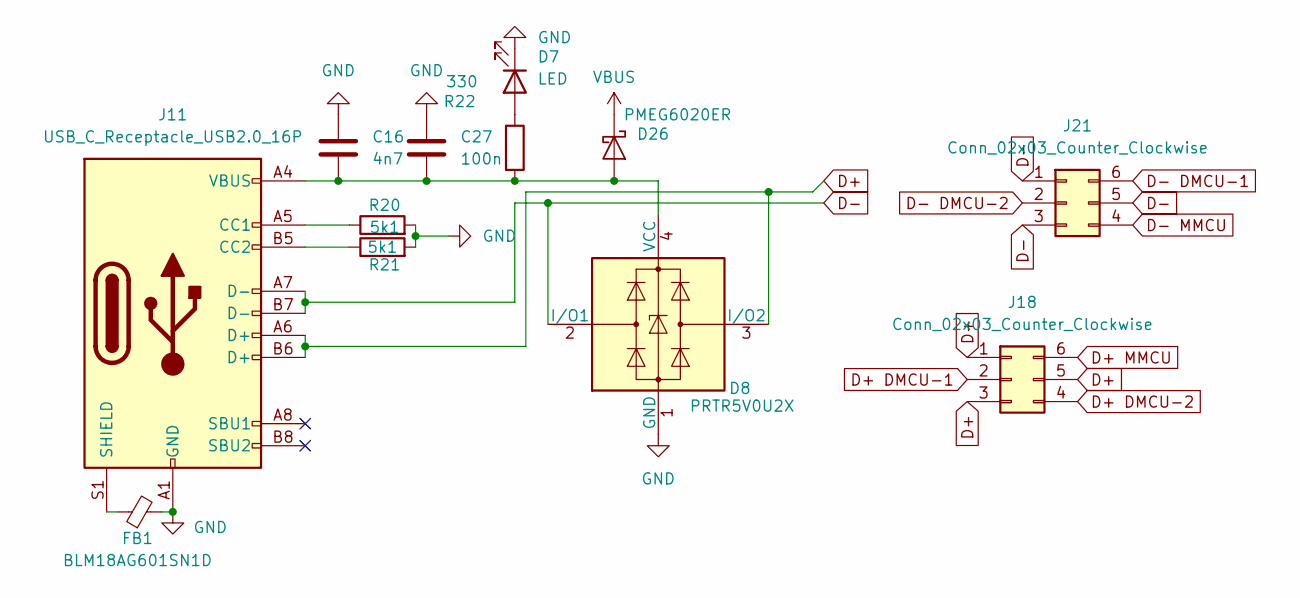
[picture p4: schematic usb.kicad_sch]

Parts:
C16: 4n7; C_0603_1608Metric
C27: 100n; C_0603_1608Metric
D7: LED; LED_0603_1608Metric
D8: PRTR5V0U2X; SOT-143
D26: PMEG6020ER; Nexperia_CFP3_SOD-123W
FB1: BLM18AG601SN1D; R_0603_1608Metric
J11: USB_C_Receptacle_USB2.0_16P; USB_C_Receptacle_GCT_USB4105-xx-A_16P_TopMnt_Horizontal
J18, J21: Conn_02x03_Counter_Clockwise; PinHeader_2x03_P2.54mm_Vertical
R20, R21: 5k1; R_0603_1608Metric
R22: 330; R_0603_1608Metric

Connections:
D+: D8.3 (I/O2), J11.A6 (D+), J11.B6 (D+), J18.1, J18.3, J18.5
D+ DMCU-1: J18.2; also elsewhere on the board
D+ DMCU-2: J18.4; also elsewhere on the board
D+ MMCU: J18.6; also elsewhere on the board
D-: D8.2 (I/O1), J11.A7 (D-), J11.B7 (D-), J21.1, J21.3, J21.5
D- DMCU-1: J21.6; also elsewhere on the board
D- DMCU-2: J21.2; also elsewhere on the board
D- MMCU: J21.4; also elsewhere on the board
GND: C16.1, C27.1, D7.1 (K), D8.1 (GND), FB1.2, J11.A1 (GND), J11.A12 (GND), J11.B1 (GND), J11.B12 (GND), R20.2, R21.2; also elsewhere on the board
unnamed: D7.2 (A), R22.1
unnamed: C16.2, C27.2, D8.4 (VCC), D26.2 (A), J11.A4 (VBUS), J11.A9 (VBUS), J11.B4 (VBUS), J11.B9 (VBUS), R22.2
unnamed: J11.A5 (CC1), R20.1
unnamed: J11.B5 (CC2), R21.1
unnamed: FB1.1, J11.S1 (SHIELD)
POWAAAA: D26.1 (K); also elsewhere on the board

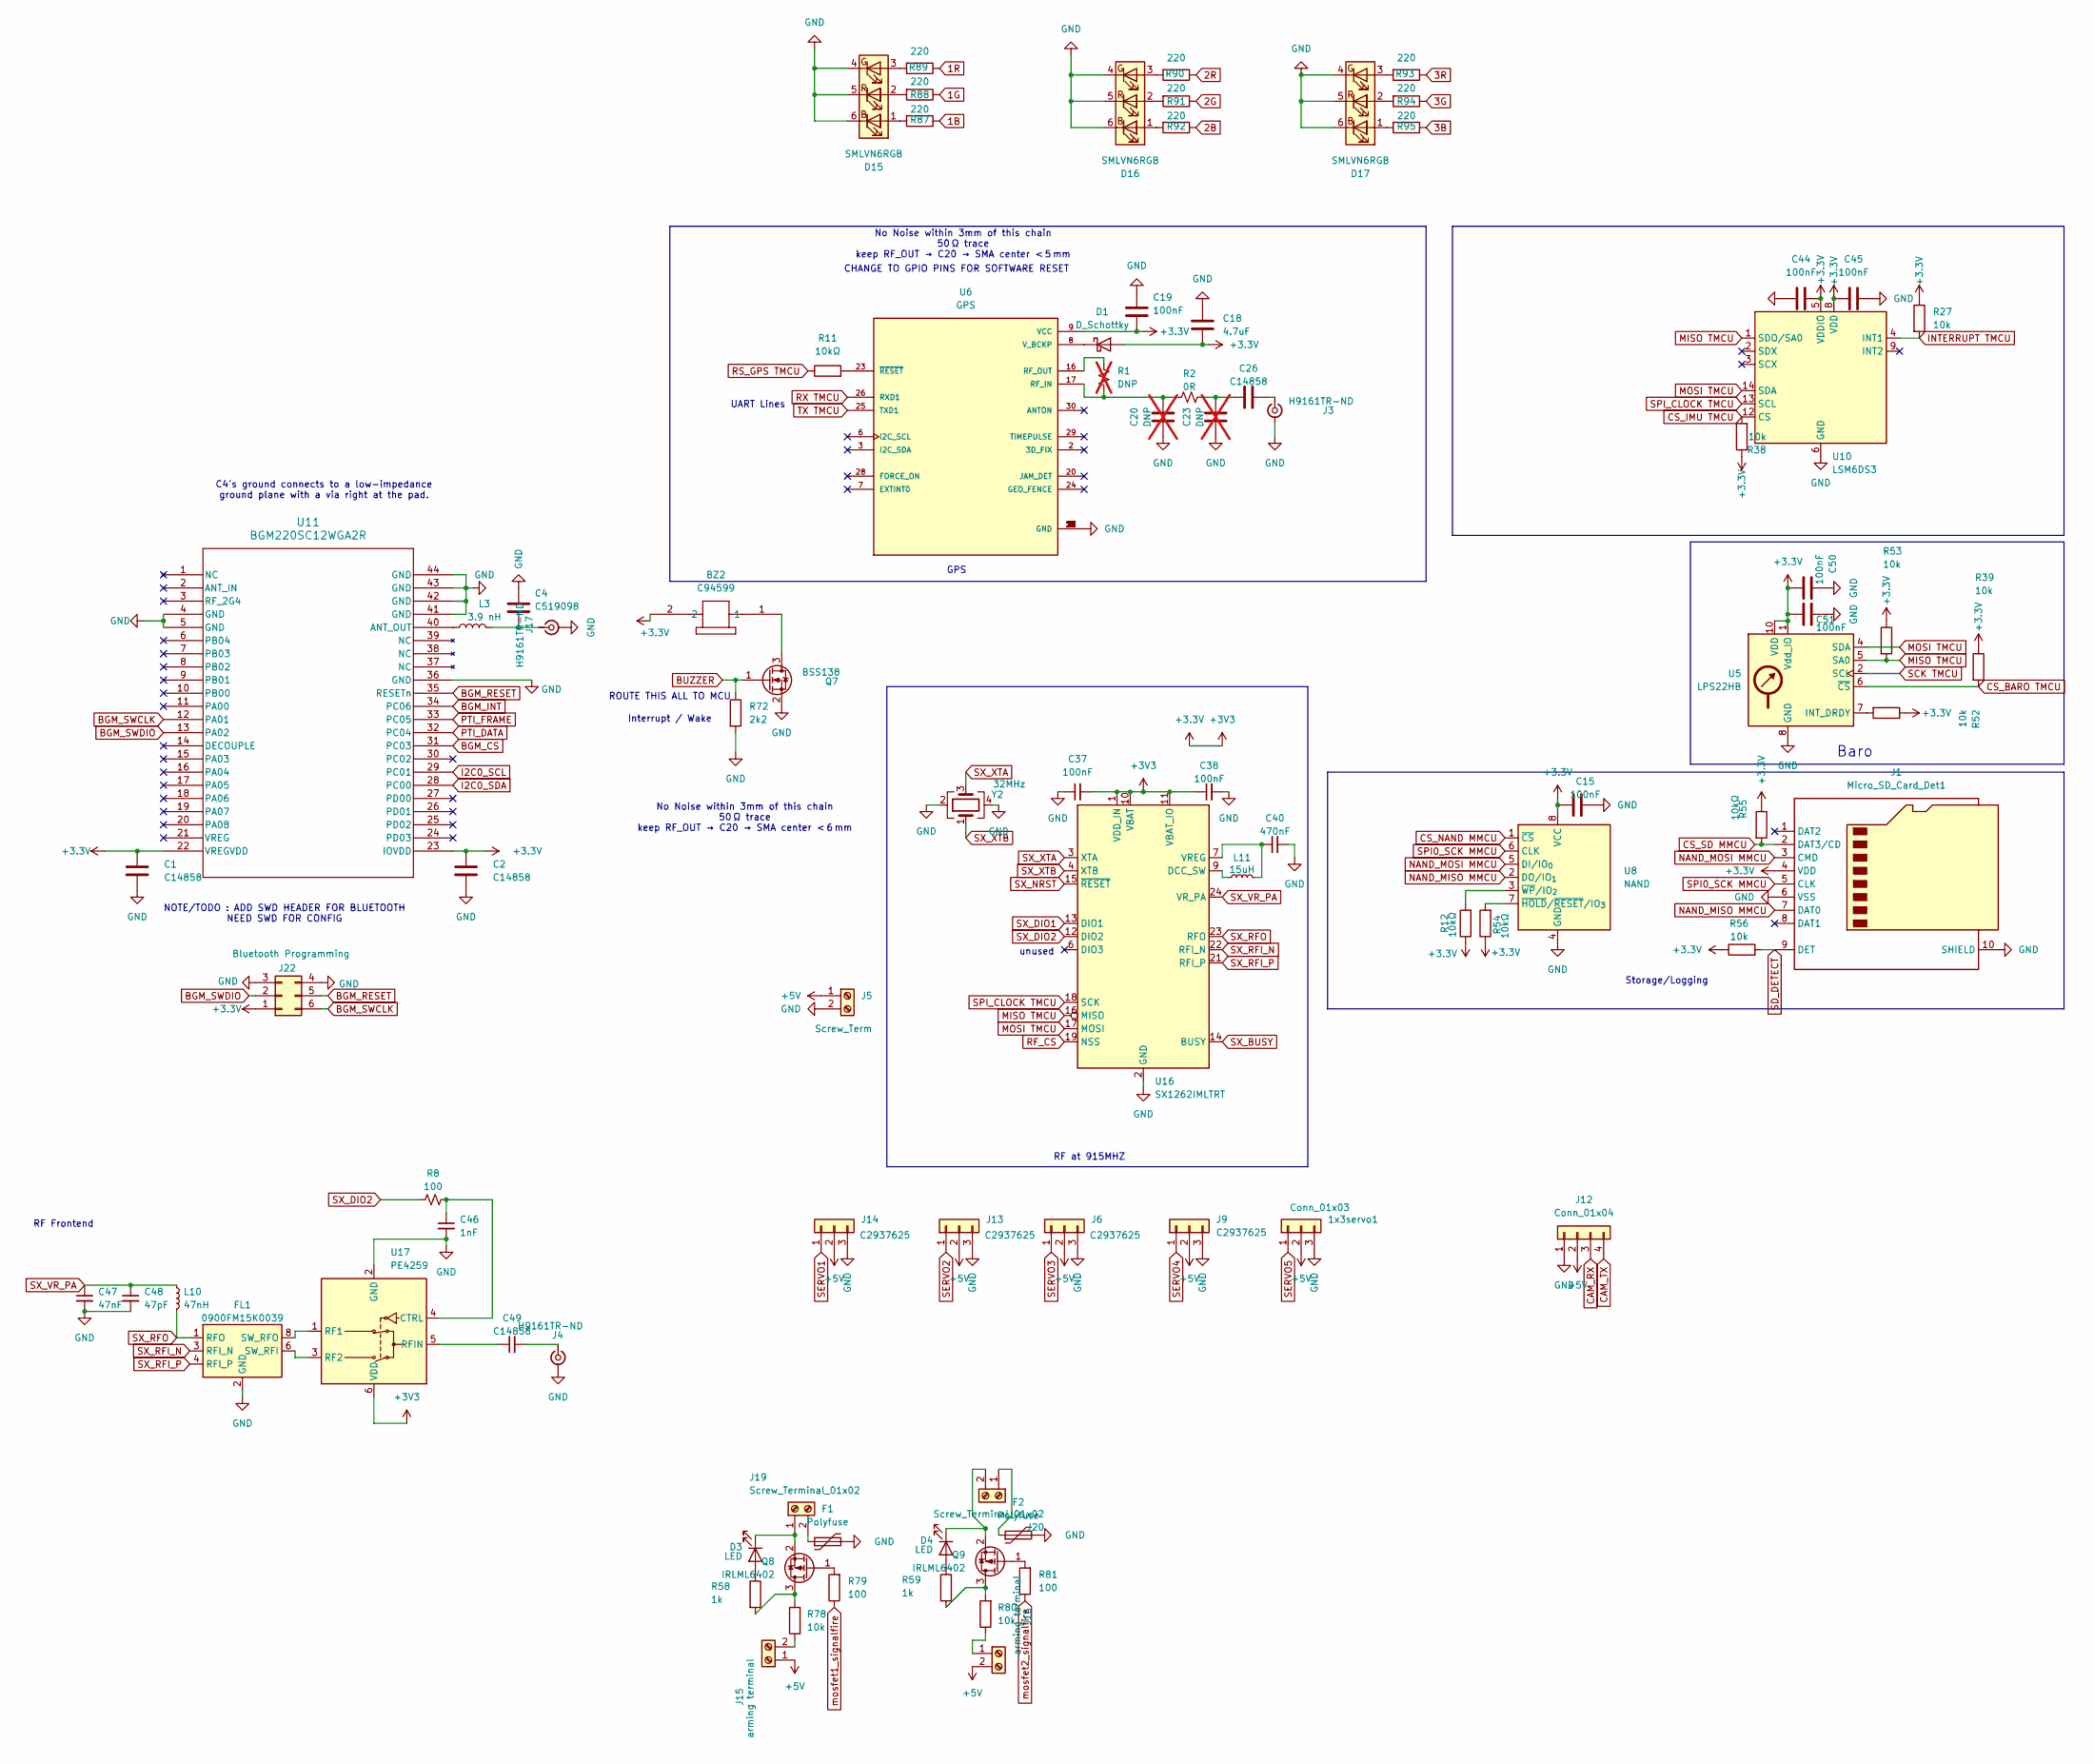
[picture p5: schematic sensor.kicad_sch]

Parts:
1x3servo1: Conn_01x03; PinHeader_1x03_P2.54mm_Vertical
BZ2: C94599; MLT-8530_JHE
C1, C2, C26: C14858; C_0603_1608Metric
C4: C519098; C_0603_1608Metric
C15, C19, C44, C45, C50, C51: 100nF; C_0603_1608Metric
C18: 4.7uF; C_0603_1608Metric
C20, C23: DNP; C_0603_1608Metric; not fitted
C37, C38: 100nF; C_0603_1608Metric; LCSC Part C14663
C40: 470nF; C_0603_1608Metric; LCSC Part C1623
C46: 1nF; C_0603_1608Metric; LCSC Part C100040
C47: 47nF; C_0603_1608Metric; LCSC Part C107093
C48: 47pF; C_0603_1608Metric; LCSC Part C105622
C49: C14858; C_0603_1608Metric; LCSC Part C14665
D1: D_Schottky; D_0603_1608Metric
D3, D4: LED; LED_0603_1608Metric
D15, D16, D17: SMLVN6RGB; LED_ROHM_SMLVN6
F1, F2: Polyfuse; Fuse_0603_1608Metric
FL1: 0900FM15K0039; Balun_Johanson_0900FM15K0039; LCSC Part C5224443
J1: Micro_SD_Card_Det1; microSD_HC_Hirose_DM3D-SF
J3, J4, J17: H9161TR-ND; U.FL_Hirose_U.FL-R-SMT-1_Vertical
J5: Screw_Term; TerminalBlock_Phoenix_MPT-0,5-2-2.54_1x02_P2.54mm_Horizontal
J6, J9, J13, J14: C2937625; PinHeader_1x03_P2.54mm_Vertical
J12: Conn_01x04; PinHeader_1x04_P2.54mm_Vertical
J15, J16: arming terminal; TerminalBlock_Phoenix_MPT-0,5-2-2.54_1x02_P2.54mm_Horizontal
J19, J20: Screw_Terminal_01x02; TerminalBlock_Phoenix_MPT-0,5-2-2.54_1x02_P2.54mm_Horizontal
J22: Bluetooth Programming; PinHeader_2x03_P2.54mm_Vertical
L3: 3.9 nH; L_0603_1608Metric
L10: 47nH; L_0603_1608Metric; LCSC Part C285885
L11: 15uH; L_0805_2012Metric; LCSC Part C383402
Q7: BSS138; SOT-23
Q8, Q9: IRLML6402; SOT-23
R1: DNP; R_0603_1608Metric; not fitted
R2: 0R; R_0603_1608Metric
R8: 100; R_0603_1608Metric; LCSC Part C105588
R11, R12, R54, R55: 10kΩ; R_0603_1608Metric
R27, R38, R39, R52, R53, R56, R78, R80: 10k; R_0603_1608Metric
R58, R59: 1k; R_0603_1608Metric
R72: 2k2; R_0603_1608Metric
R79, R81: 100; R_0603_1608Metric
R87, R88, R89, R90, R91, R92, R93, R94, R95: 220; R_0603_1608Metric
U5: LPS22HB; ST_HLGA-10_2x2mm_P0.5mm_LayoutBorder3x2y
U6: GPS; Quectel_L96; DigiKey_Part_Number 2958-L96-M33TR-ND
U8: NAND; SOIC-8_5.3x5.3mm_P1.27mm
U10: LSM6DS3; LGA-14_3x2.5mm_P0.5mm_LayoutBorder3x4y
U11: BGM220SC12WGA2R; BGM220S_SIL
U16: SX1262IMLTRT; QFN-24-1EP_4x4mm_P0.5mm_EP2.6x2.6mm; LCSC Part C191341
U17: PE4259; SOT-363_SC-70-6; LCSC Part C470892
Y2: 32MHz; Crystal_SMD_3225-4Pin_3.2x2.5mm; LCSC Part C37635386

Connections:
1B: R87.1; also elsewhere on the board
1G: R88.1; also elsewhere on the board
1R: R89.1; also elsewhere on the board
2B: R92.1; also elsewhere on the board
2G: R91.1; also elsewhere on the board
2R: R90.1; also elsewhere on the board
3B: R95.1; also elsewhere on the board
3G: R94.1; also elsewhere on the board
3R: R93.1; also elsewhere on the board
+3.3V: BZ2.2, C1.2, C2.2, C15.1, C18.2, C19.2, C37.2, C38.1, C44.2, C45.2, C50.2, C51.2, D1.2 (A), J1.4 (VDD), J22.1, R12.1, R27.1, R38.1, R39.1, R52.1, R53.1, R54.1, R55.1, R56.1, U5.1 (Vdd_IO), U5.10 (VDD), U6.9 (VCC), U8.8 (VCC), U10.5 (VDDIO), U10.8 (VDD), U11.22 (VREGVDD), U11.23 (IOVDD), U16.1 (VDD_IN), U16.10 (VBAT), U16.11 (VBAT_IO), U17.6 (VDD); also elsewhere on the board
+5V: 1x3servo1.2, J5.1, J6.2, J9.2, J12.2, J13.2, J14.2, J15.1, J16.2; also elsewhere on the board
BGM_CS: U11.31 (PC03); also elsewhere on the board
BGM_INT: U11.34 (PC06); also elsewhere on the board
BGM_RESET: J22.5, U11.35 (RESETn); also elsewhere on the board
BGM_SWCLK: J22.6, U11.12 (PA01)
BGM_SWDIO: J22.2, U11.13 (PA02)
BUZZER: Q7.1 (G), R72.1; also elsewhere on the board
CAM_RX: J12.3; also elsewhere on the board
CAM_TX: J12.4; also elsewhere on the board
CS_BARO TMCU: R39.2, U5.6 (~CS); also elsewhere on the board
CS_IMU TMCU: R38.2, U10.12 (CS); also elsewhere on the board
CS_NAND MMCU: U8.1 (~CS); also elsewhere on the board
CS_SD MMCU: J1.2 (DAT3/CD), R55.2; also elsewhere on the board
GND: 1x3servo1.3, C1.1, C2.1, C4.1, C15.2, C18.1, C19.1, C20.2, C23.2, C37.1, C38.2, C40.2, C44.1, C45.1, C46.2, C47.2, C48.2, C50.1, C51.1, D15.4 (GK), D15.5 (RK), D15.6 (BK), D16.4 (GK), D16.5 (RK), D16.6 (BK), D17.4 (GK), D17.5 (RK), D17.6 (BK), F1.2, F2.2, FL1.2 (GND), FL1.5 (GND), FL1.7 (GND), FL1.9 (GND), FL1.10 (GND), J1.6 (VSS), J1.10 (SHIELD), J3.2 (Ext), J4.2 (Ext), J5.2, J6.3, J9.3, J12.1, J13.3, J14.3, J17.2 (Ext), J22.3, J22.4, Q7.2 (S), R72.2, U5.3 (GND), U5.8 (GND), U5.9 (GND), U6.4 (GND), U6.5 (GND), U6.10 (GND), U6.11 (GND), U6.12 (GND), U6.13 (GND), U6.14 (GND), U6.15 (GND), U6.18 (GND), U6.19 (GND), U6.21 (GND), U6.22 (GND), U6.27 (GND), U6.31 (GND), U8.4 (GND), U10.6 (GND), U10.7 (GND), U11.4 (GND), U11.5 (GND), U11.36 (GND), U11.41 (GND), U11.42 (GND), U11.43 (GND), U11.44 (GND), U16.2 (GND), U16.5 (GND), U16.8 (GND), U16.20 (GND), U16.25 (GND), U17.2 (GND), Y2.2, Y2.4; also elsewhere on the board
I2C0_SCL: U11.29 (PC01); also elsewhere on the board
I2C0_SDA: U11.28 (PC00); also elsewhere on the board
INTERRUPT TMCU: R27.2, U10.4 (INT1); also elsewhere on the board
MISO TMCU: R53.2, U5.5 (SA0), U10.1 (SDO/SA0), U16.16 (MISO); also elsewhere on the board
MOSI TMCU: U5.4 (SDA), U10.14 (SDA), U16.17 (MOSI); also elsewhere on the board
NAND_MISO MMCU: J1.7 (DAT0), U8.2 (DO/IO_{1}); also elsewhere on the board
NAND_MOSI MMCU: J1.3 (CMD), U8.5 (DI/IO_{0}); also elsewhere on the board
unnamed: C23.1, C26.2, R2.2
unnamed: D1.1 (K), U6.8 (V_BCKP)
unnamed: D3.2 (A), R58.1
unnamed: D3.1 (K), J19.1, Q8.2 (S)
unnamed: D4.2 (A), R59.1
unnamed: D4.1 (K), J20.2, Q9.2 (S)
unnamed: D15.1 (BA), R87.2
unnamed: D15.3 (GA), R89.2
unnamed: D15.2 (RA), R88.2
unnamed: D16.1 (BA), R92.2
unnamed: D16.3 (GA), R90.2
unnamed: D16.2 (RA), R91.2
unnamed: D17.1 (BA), R95.2
unnamed: D17.3 (GA), R93.2
unnamed: D17.2 (RA), R94.2
unnamed: FL1.6 (SW_RFI), U17.3 (RF2)
unnamed: FL1.8 (SW_RFO), U17.1 (RF1)
unnamed: C26.1, J3.1 (In)
unnamed: C49.2, J4.1 (In)
unnamed: J15.2, R78.1
unnamed: J16.1, R80.1
unnamed: C4.2, J17.1 (In), L3.2
unnamed: F1.1, J19.2
unnamed: F2.1, J20.1
unnamed: BZ2.1, Q7.3 (D)
unnamed: Q8.3 (D), R58.2, R78.2
unnamed: Q8.1 (G), R79.2
unnamed: Q9.3 (D), R59.2, R80.2
unnamed: Q9.1 (G), R81.2
unnamed: R52.2, U5.7 (INT_DRDY)
unnamed: C20.1, R1.2, R2.1, U6.17 (RF_IN)
unnamed: R1.1, U6.16 (RF_OUT)
unnamed: R11.2, U6.23 (~RESET)
unnamed: R54.2, U8.7 (~HOLD/~RESET/IO_{3})
unnamed: R12.2, U8.3 (~WP/IO_{2})
unnamed: L3.1, U11.40 (ANT_OUT)
unnamed: L11.1, U16.9 (DCC_SW)
unnamed: C40.1, L11.2, U16.7 (VREG)
unnamed: C46.1, R8.2, U17.4 (CTRL)
unnamed: C49.1, U17.5 (RFIN)
PTI_DATA: U11.32 (PC04)
PTI_FRAME: U11.33 (PC05)
RF_CS: U16.19 (NSS); also elsewhere on the board
RS_GPS TMCU: R11.1; also elsewhere on the board
RX TMCU: U6.26 (RXD1); also elsewhere on the board
SCK TMCU: U5.2 (SCL); also elsewhere on the board
SD_DETECT: J1.9 (DET), R56.2
SERVO1: J14.1; also elsewhere on the board
SERVO2: J13.1; also elsewhere on the board
SERVO3: J6.1; also elsewhere on the board
SERVO4: J9.1; also elsewhere on the board
SERVO5: 1x3servo1.1; also elsewhere on the board
SPI0_SCK MMCU: J1.5 (CLK), U8.6 (CLK); also elsewhere on the board
SPI_CLOCK TMCU: U10.13 (SCL), U16.18 (SCK); also elsewhere on the board
SX_BUSY: U16.14 (BUSY)
SX_DIO1: U16.13 (DIO1); also elsewhere on the board
SX_DIO2: R8.1, U16.12 (DIO2)
SX_NRST: U16.15 (~RESET); also elsewhere on the board
SX_RFI_N: FL1.3 (RFI_N), U16.22 (RFI_N)
SX_RFI_P: FL1.4 (RFI_P), U16.21 (RFI_P)
SX_RFO: FL1.1 (RFO), L10.2, U16.23 (RFO)
SX_VR_PA: C47.1, C48.1, L10.1, U16.24 (VR_PA)
SX_XTA: U16.3 (XTA), Y2.3
SX_XTB: U16.4 (XTB), Y2.1
TX TMCU: U6.25 (TXD1); also elsewhere on the board
mosfet1_signalfire: R79.1; also elsewhere on the board
mosfet2_signalfire: R81.1; also elsewhere on the board

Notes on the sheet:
GPS
UART Lines
C4's ground connects to a low-impedance ground plane with a via right at the pad.
NOTE/TODO : ADD SWD HEADER FOR BLUETOOTH NEED SWD FOR CONFIG
Storage/Logging
unused
CHANGE TO GPIO PINS FOR SOFTWARE RESET
ROUTE THIS ALL TO MCU
Baro
Interrupt / Wake
No Noise within 3mm of this chain 50 Ω trace keep RF_OUT → C20 → SMA center < 6 mm
RF Frontend
RF at 915MHZ
No Noise within 3mm of this chain 50 Ω trace keep RF_OUT → C20 → SMA center < 5 mm

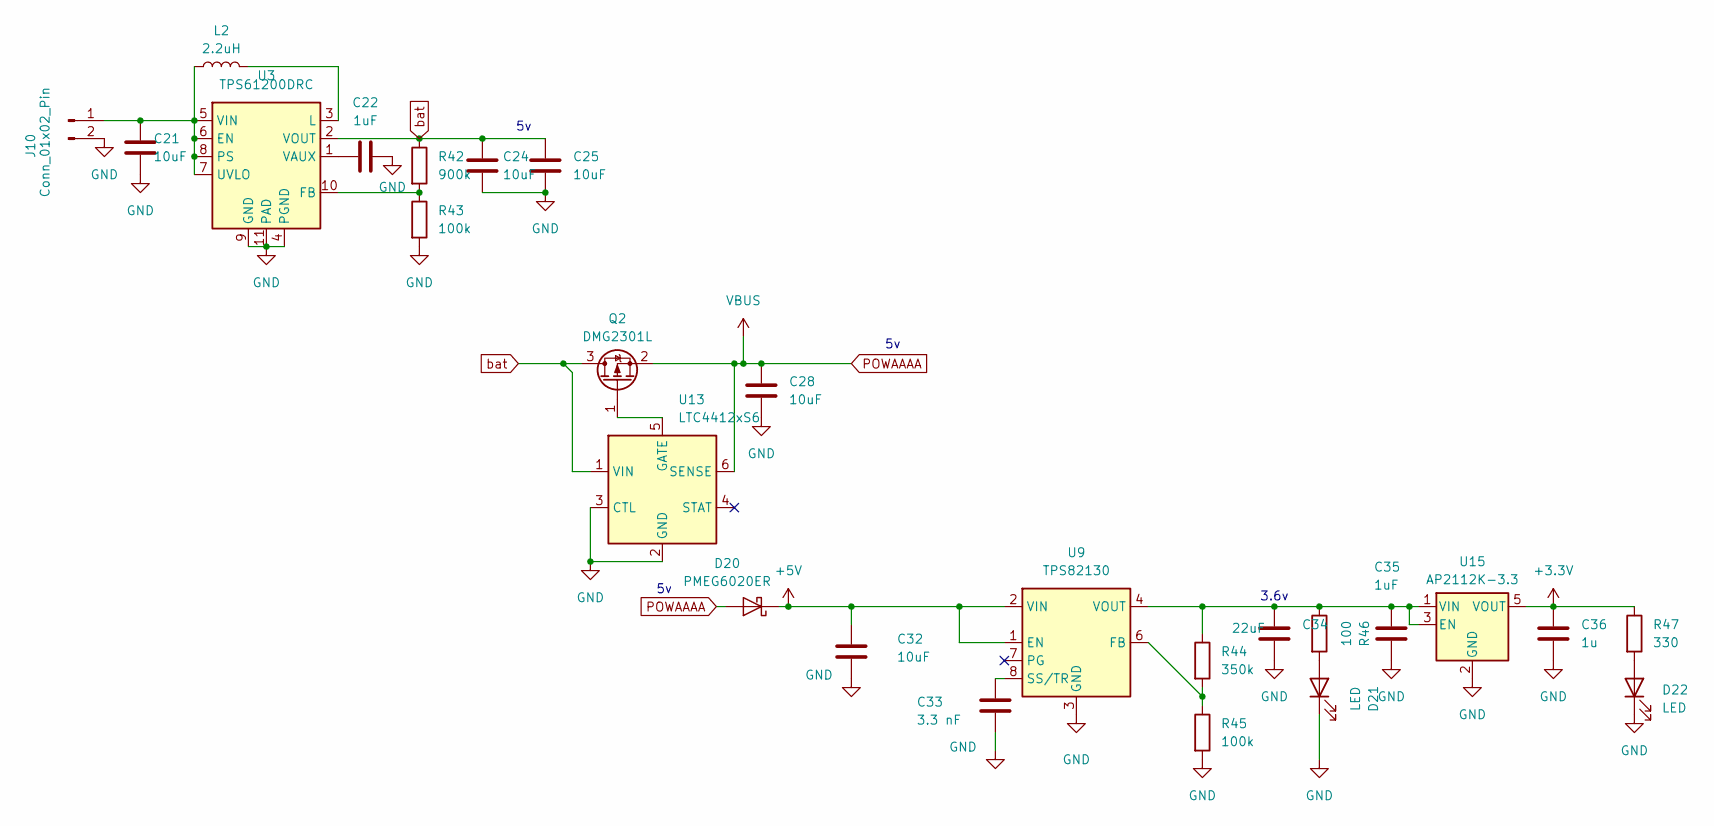
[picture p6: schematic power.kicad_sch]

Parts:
C21, C24, C25, C28, C32: 10uF; C_0603_1608Metric
C22, C35: 1uF; C_0603_1608Metric
C33: 3.3 nF; C_0603_1608Metric
C34: 22uF; C_0603_1608Metric
C36: 1u; C_0603_1608Metric
D20: PMEG6020ER; Nexperia_CFP3_SOD-123W
D21, D22: LED; LED_0603_1608Metric
J10: Conn_01x02_Pin; TerminalBlock_Phoenix_MPT-0,5-2-2.54_1x02_P2.54mm_Horizontal
L2: 2.2uH; L_APV_ANR4018
Q2: DMG2301L; SOT-23
R42: 900k; R_0603_1608Metric
R43, R45: 100k; R_0603_1608Metric
R44: 350k; R_0603_1608Metric
R46: 100; R_0603_1608Metric
R47: 330; R_0603_1608Metric
U3: TPS61200DRC; Texas_S-PVSON-N10_ThermalVias
U9: TPS82130; Texas_SIL0008D_MicroSiP-8-1EP_2.8x3mm_P0.65mm_EP1.1x1.9mm_T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
U13: LTC4412xS6; TSOT-23-6
U15: AP2112K-3.3; SOT-23-5

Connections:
+3.3V: C36.1, R47.1, U15.5 (VOUT); also elsewhere on the board
+5V: C32.1, D20.1 (K), U9.1 (EN), U9.2 (VIN); also elsewhere on the board
GND: C21.2, C22.2, C24.2, C25.2, C28.2, C32.2, C33.2, C34.2, C35.2, C36.2, D21.1 (K), D22.1 (K), J10.2, R43.2, R45.2, U3.4 (PGND), U3.9 (GND), U3.11 (PAD), U9.3 (GND), U9.9 (GND), U13.2 (GND), U13.3 (CTL), U15.2 (GND); also elsewhere on the board
unnamed: D21.2 (A), R46.2
unnamed: D22.2 (A), R47.2
unnamed: C21.1, J10.1, L2.1, U3.5 (VIN), U3.6 (EN), U3.7 (UVLO), U3.8 (PS)
unnamed: Q2.1 (G), U13.5 (GATE)
unnamed: R42.2, R43.1, U3.10 (FB)
unnamed: L2.2, U3.3 (L)
unnamed: C22.1, U3.1 (VAUX)
unnamed: R44.2, R45.1, U9.6 (FB)
unnamed: C33.1, U9.8 (SS/TR)
unnamed: C34.1, C35.1, R44.1, R46.1, U9.4 (VOUT), U9.5 (VOUT), U15.1 (VIN), U15.3 (EN)
POWAAAA: C28.1, D20.2 (A), Q2.2 (S), U13.6 (SENSE); also elsewhere on the board
bat: C24.1, C25.1, Q2.3 (D), R42.1, U3.2 (VOUT), U13.1 (VIN)

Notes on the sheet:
3.6v

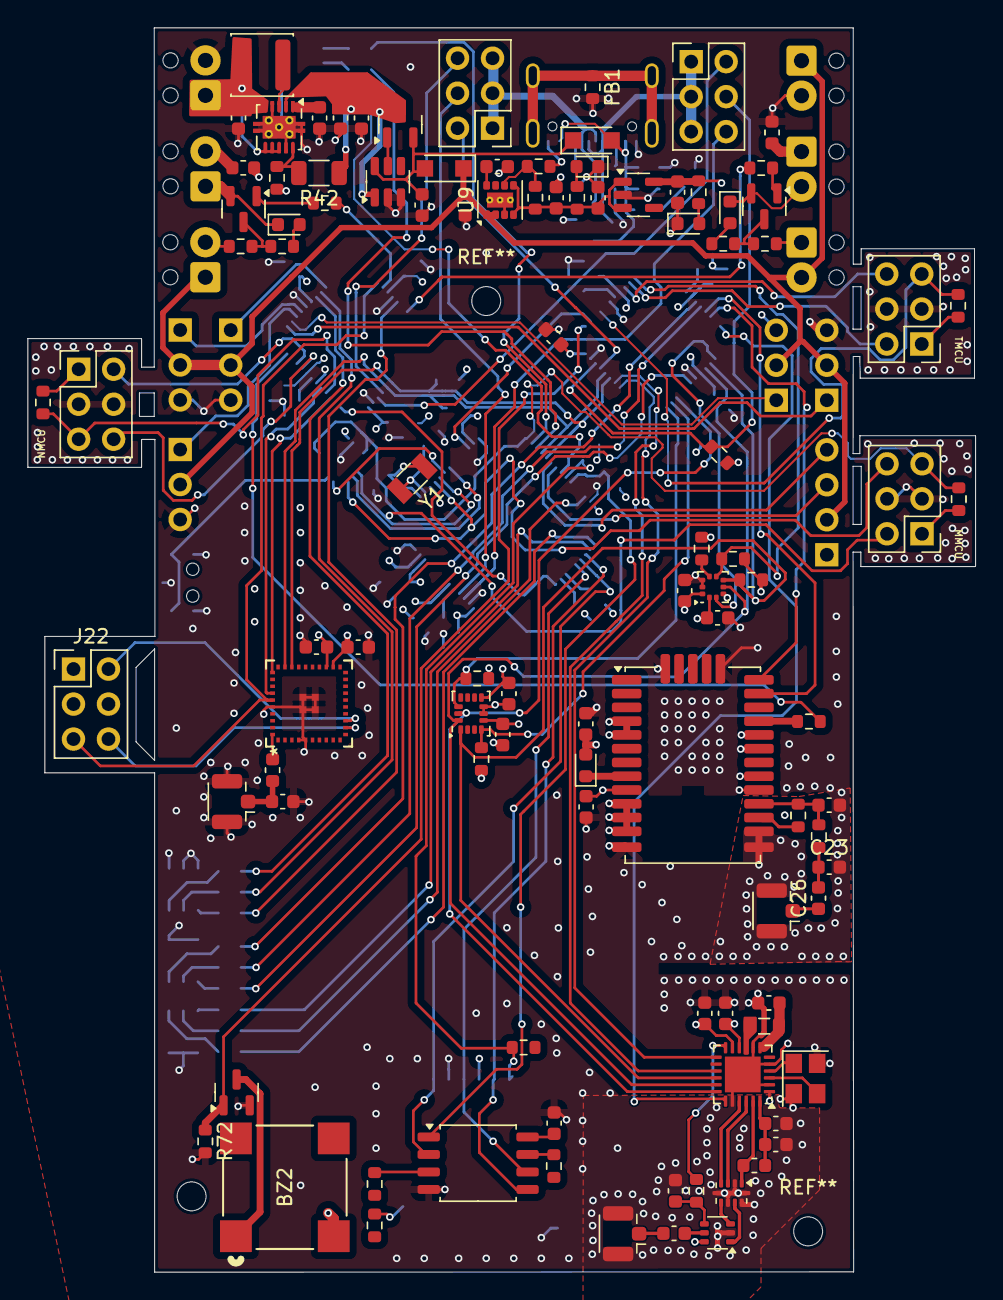
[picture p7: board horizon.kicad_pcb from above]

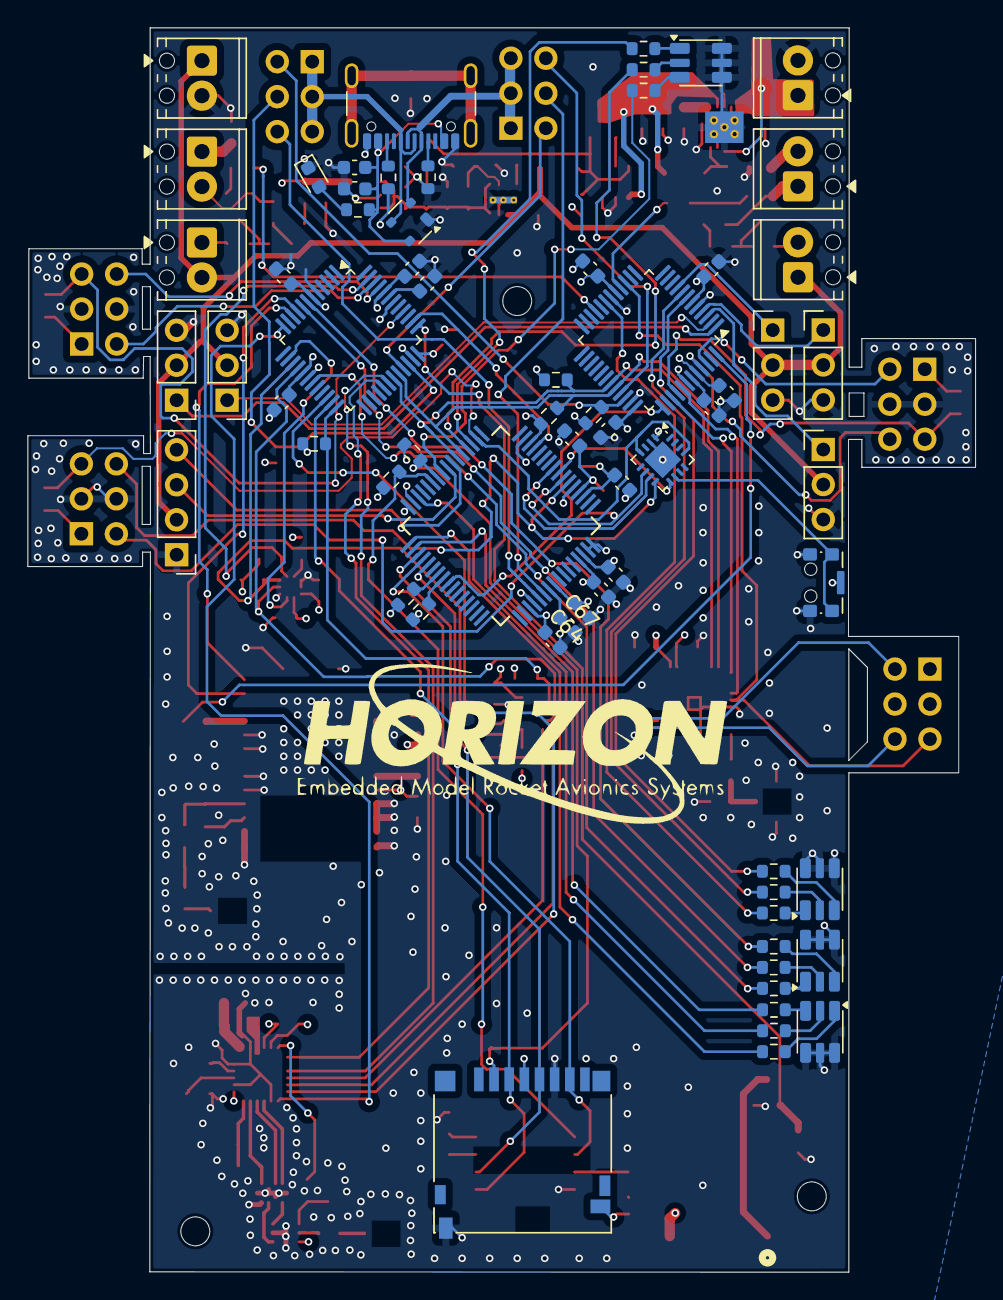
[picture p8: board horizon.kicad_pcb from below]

Board: 4 copper layers, 68.8 x 90.3 mm, 169 parts (66 on the bottom side), 147 nets.

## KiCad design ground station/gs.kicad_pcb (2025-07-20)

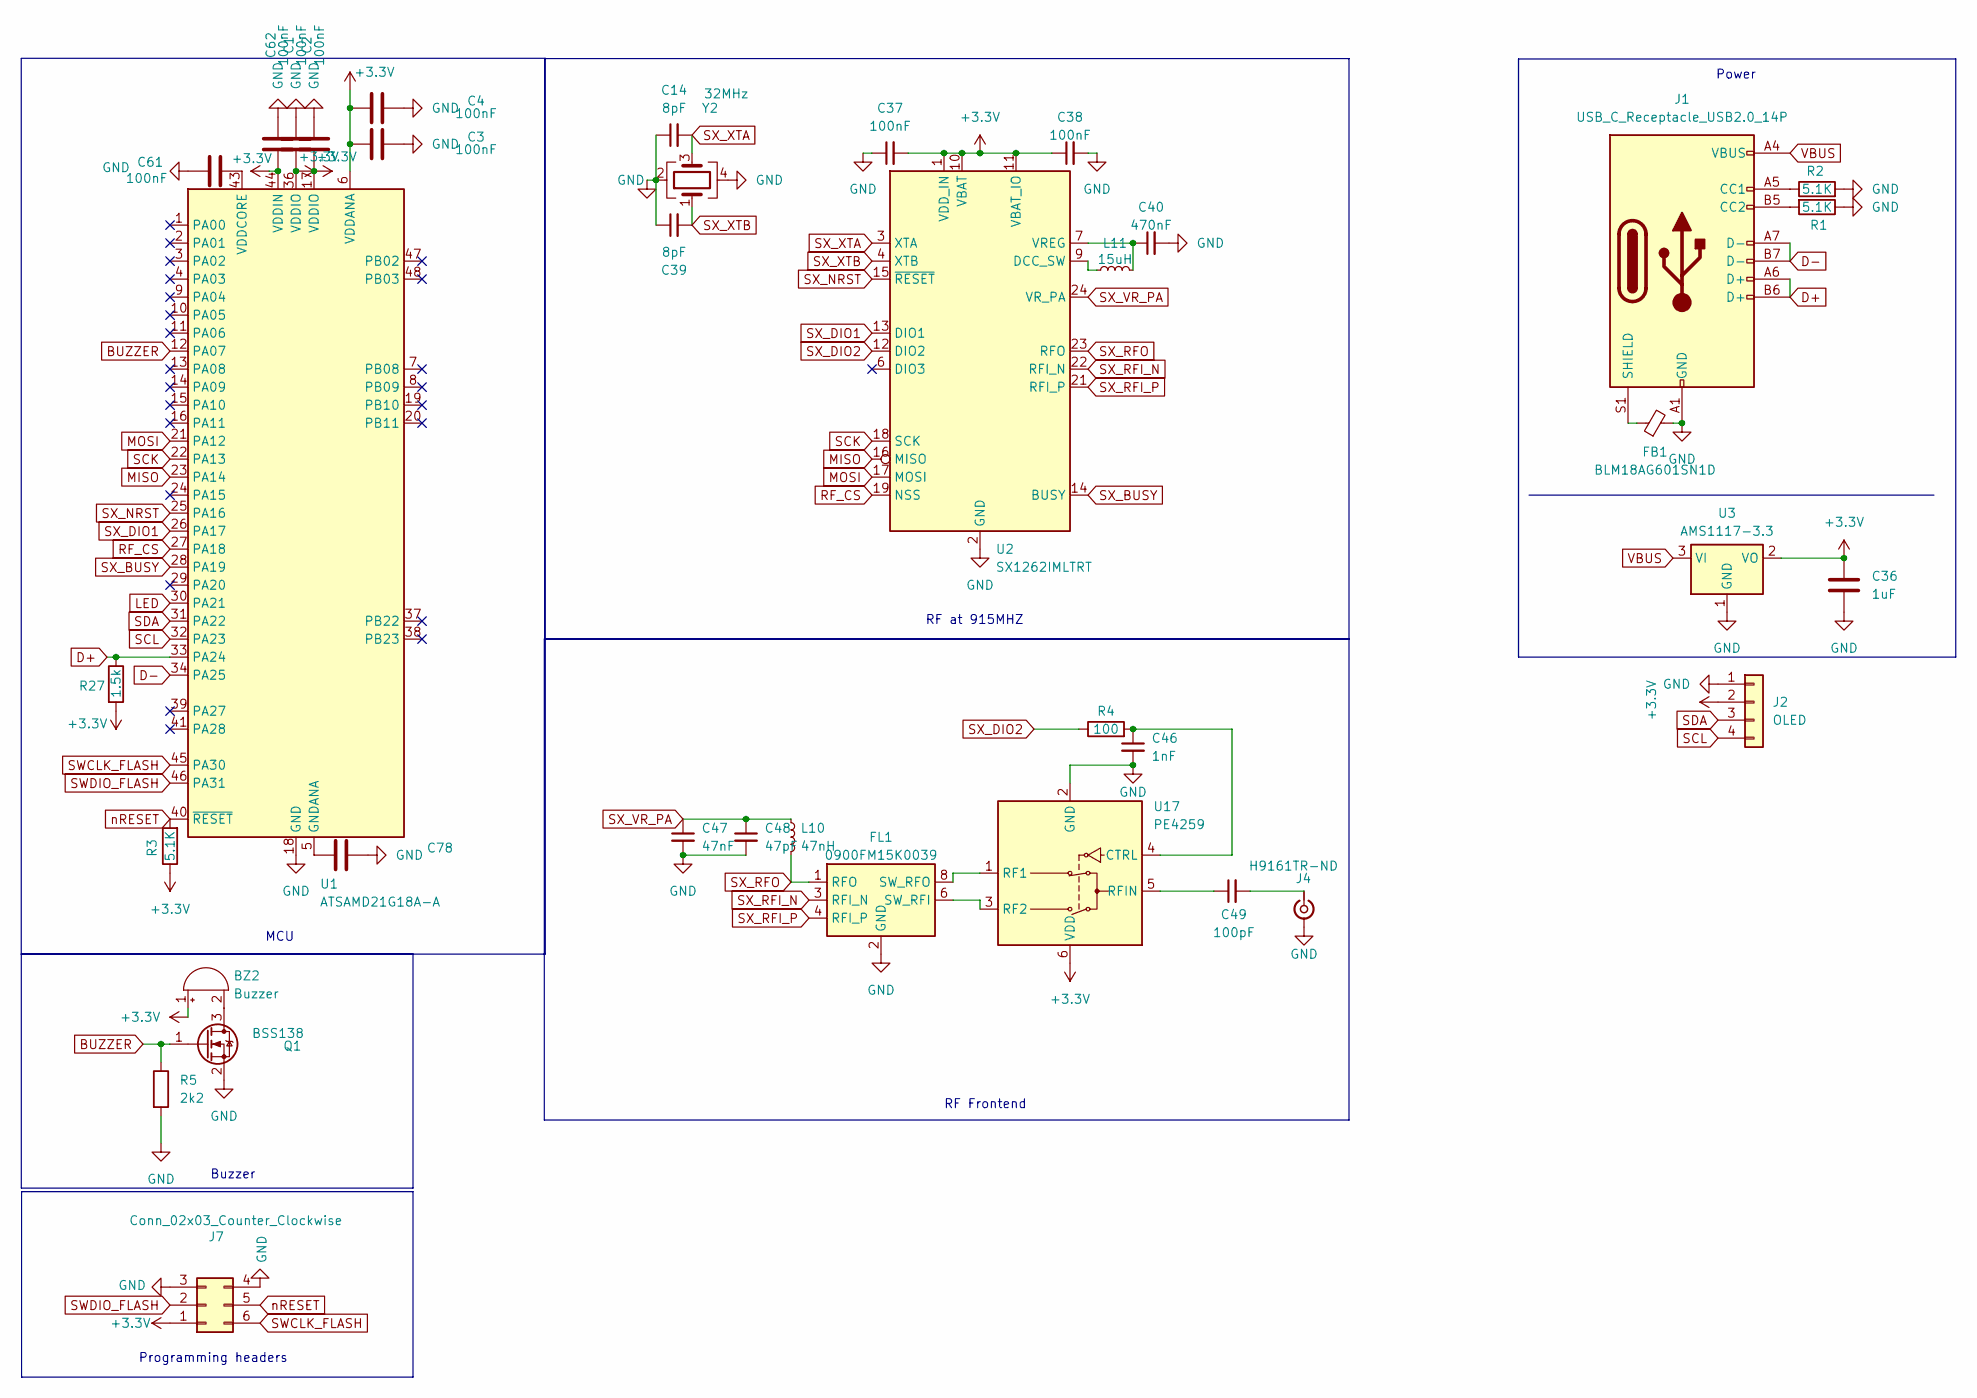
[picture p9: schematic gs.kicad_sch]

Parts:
BZ2: Buzzer; MagneticBuzzer_PUI_AT-0927-TT-6-R
C1, C2, C3, C4, C61, C62, C78: 100nF; C_0603_1608Metric
C14, C39: 8pF; C_0603_1608Metric; LCSC Part C327316
C36: 1uF; C_0603_1608Metric
C37, C38: 100nF; C_0603_1608Metric; LCSC Part C14663
C40: 470nF; C_0603_1608Metric; LCSC Part C1623
C46: 1nF; C_0603_1608Metric; LCSC Part C100040
C47: 47nF; C_0603_1608Metric; LCSC Part C107093
C48: 47pF; C_0603_1608Metric; LCSC Part C105622
C49: 100pF; C_0603_1608Metric; LCSC Part C14665
FB1: BLM18AG601SN1D; R_0603_1608Metric; LCSC Part C19330
FL1: 0900FM15K0039; Balun_Johanson_0900FM15K0039; LCSC Part C5224443
J1: USB_C_Receptacle_USB2.0_14P; USB_C_Receptacle_HCTL_HC-TYPE-C-16P-01A
J2: OLED; NS-Tech_Grove_1x04_P2mm_Vertical
J4: H9161TR-ND; U.FL_Hirose_U.FL-R-SMT-1_Vertical
J7: Conn_02x03_Counter_Clockwise; PinHeader_2x03_P2.54mm_Vertical
L10: 47nH; L_0603_1608Metric; LCSC Part C285885
L11: 15uH; L_0805_2012Metric; LCSC Part C383402
Q1: BSS138; SOT-23
R1, R2, R3: 5.1K; C_0603_1608Metric
R4: 100; R_0603_1608Metric
R5: 2k2; R_0603_1608Metric
R27: 1.5k; R_0603_1608Metric
U1: ATSAMD21G18A-A; TQFP-48_7x7mm_P0.5mm
U2: SX1262IMLTRT; QFN-24-1EP_4x4mm_P0.5mm_EP2.6x2.6mm
U3: AMS1117-3.3; SOT-223-3_TabPin2
U17: PE4259; SOT-363_SC-70-6; LCSC Part C470892
Y2: 32MHz; Crystal_SMD_3225-4Pin_3.2x2.5mm; LCSC Part C37635386

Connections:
+3.3V: BZ2.1 (+), C1.2, C2.2, C3.2, C4.2, C36.1, C37.2, C38.1, C62.2, J2.2, J7.1, R3.1, R27.2, U1.6 (VDDANA), U1.17 (VDDIO), U1.36 (VDDIO), U1.44 (VDDIN), U2.1 (VDD_IN), U2.10 (VBAT), U2.11 (VBAT_IO), U3.2 (VO), U17.6 (VDD)
BUZZER: Q1.1 (G), R5.1, U1.12 (PA07)
D+: J1.A6 (D+), J1.B6 (D+), R27.1, U1.33 (PA24)
D-: J1.A7 (D-), J1.B7 (D-), U1.34 (PA25)
GND: C1.1, C2.1, C3.1, C4.1, C14.1, C36.2, C37.1, C38.2, C39.1, C40.2, C46.2, C47.2, C48.2, C61.1, C62.1, C78.1, FB1.2, FL1.2 (GND), FL1.5 (GND), FL1.7 (GND), FL1.9 (GND), FL1.10 (GND), J1.A1 (GND), J1.A12 (GND), J1.B1 (GND), J1.B12 (GND), J2.1, J4.2 (Ext), J7.3, J7.4, Q1.2 (S), R1.1, R2.2, R5.2, U1.18 (GND), U1.35 (GND), U1.42 (GND), U2.2 (GND), U2.5 (GND), U2.8 (GND), U2.20 (GND), U2.25 (GND), U3.1 (GND), U17.2 (GND), Y2.2, Y2.4
LED: U1.30 (PA21)
MISO: U1.23 (PA14), U2.16 (MISO)
MOSI: U1.21 (PA12), U2.17 (MOSI)
unnamed: BZ2.2 (-), Q1.3 (D)
unnamed: FL1.6 (SW_RFI), U17.3 (RF2)
unnamed: FL1.8 (SW_RFO), U17.1 (RF1)
unnamed: J1.A5 (CC1), R2.1
unnamed: J1.B5 (CC2), R1.2
unnamed: FB1.1, J1.S1 (SHIELD)
unnamed: C49.2, J4.1 (In)
unnamed: C78.2, U1.5 (GNDANA)
unnamed: C61.2, U1.43 (VDDCORE)
unnamed: L11.1, U2.9 (DCC_SW)
unnamed: C40.1, L11.2, U2.7 (VREG)
unnamed: C46.1, R4.2, U17.4 (CTRL)
unnamed: C49.1, U17.5 (RFIN)
RF_CS: U1.27 (PA18), U2.19 (NSS)
SCK: U1.22 (PA13), U2.18 (SCK)
SCL: J2.4, U1.32 (PA23)
SDA: J2.3, U1.31 (PA22)
SWCLK_FLASH: J7.6, U1.45 (PA30)
SWDIO_FLASH: J7.2, U1.46 (PA31)
SX_BUSY: U1.28 (PA19), U2.14 (BUSY)
SX_DIO1: U1.26 (PA17), U2.13 (DIO1)
SX_DIO2: R4.1, U2.12 (DIO2)
SX_NRST: U1.25 (PA16), U2.15 (~RESET)
SX_RFI_N: FL1.3 (RFI_N), U2.22 (RFI_N)
SX_RFI_P: FL1.4 (RFI_P), U2.21 (RFI_P)
SX_RFO: FL1.1 (RFO), L10.2, U2.23 (RFO)
SX_VR_PA: C47.1, C48.1, L10.1, U2.24 (VR_PA)
SX_XTA: C14.2, U2.3 (XTA), Y2.3
SX_XTB: C39.2, U2.4 (XTB), Y2.1
VBUS: J1.A4 (VBUS), J1.A9 (VBUS), J1.B4 (VBUS), J1.B9 (VBUS), U3.3 (VI)
nRESET: J7.5, R3.2, U1.40 (~RESET)

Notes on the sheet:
Programming headers
Buzzer
RF at 915MHZ
RF Frontend
Power
MCU

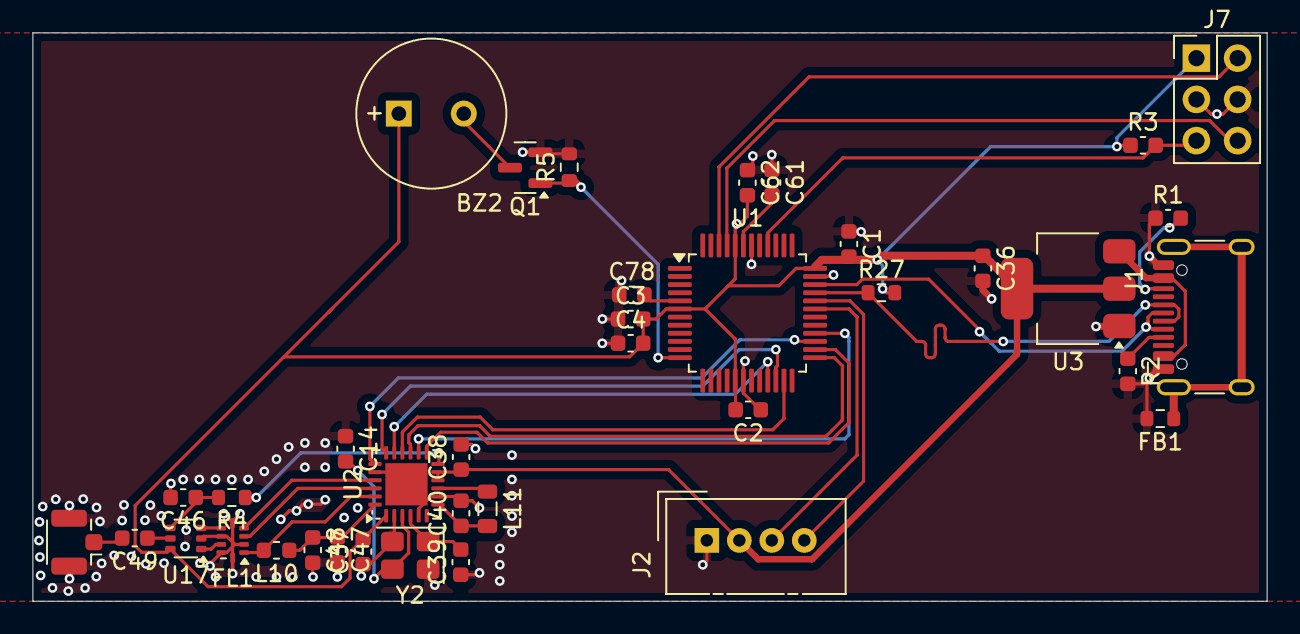
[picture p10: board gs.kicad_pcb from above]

Board: 2 copper layers, 76.0 x 35.0 mm, 38 parts (0 on the bottom side), 38 nets.

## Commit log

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2025-05-11 Added a start to the README and renamed some parts in KiCad
    [horizon.kicad_sch]
2025-05-11 input usb and random references
    [horizon.kicad_sch]
2025-05-12 idk what I changed
    [horizon.kicad_pcb]
2025-05-13 usbc changes + voltage reg
    [horizon.kicad_sch]
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2025-05-14 changes to power regulation
    [horizon.kicad_sch]
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2025-05-14 Finished with the headers
    [horizon.kicad_sch]
2025-05-14 data + bootloader pins
    [horizon.kicad_sch]
2025-05-14 switch for programming, data lines
    [horizon.kicad_sch]
2025-05-14 Added IMU Schematics and connected it to TMU via SPI
    [horizon.kicad_sch]
2025-05-14 Added like 1/3 of the GPS Schematic
    [horizon.kicad_sch]
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2025-05-14 SD Card is Done
    [horizon.kicad_sch]
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2025-05-15 Changes, idr what though :(
    [horizon.kicad_sch, power.kicad_sch, sensor.kicad_sch]
2025-05-15 misc fixes
    [horizon.kicad_sch, power.kicad_sch, sensor.kicad_sch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]
2025-05-15 GPS is done! yay
    [sensor.kicad_sch]
2025-05-15 RF at 915MHZ done!
    [sensor.kicad_sch]
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2025-05-16 chip wiring fix
    [horizon.kicad_sch, sensor.kicad_sch]
2025-05-16 servo mosfet, pyro mosfet, camera
    [horizon.kicad_sch, sensor.kicad_sch]
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2025-05-16 fixed wiring stuff and accessories
    [horizon.kicad_sch, sensor.kicad_sch]
2025-05-16 Movement changes for PCB
    [horizon.kicad_pcb]
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2025-05-16 Trying to add GPS footprint
    [horizon.kicad_pcb, sensor.kicad_sch]
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2025-05-18 Hopefully added BL, and all the remaining footprints
    [horizon.kicad_pcb, horizon.kicad_sch, sensor.kicad_sch]
2025-05-18 Added most of the 3d models
    [horizon.kicad_pcb]
2025-05-18 pcb parts all wired
    [horizon.kicad_pcb, sensor.kicad_sch]
2025-05-18 Merged Fix of Schematic and PCB
    [horizon.kicad_pcb, sensor.kicad_sch]
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2025-05-18 CS, and SCK for RF
    [horizon.kicad_sch, sensor.kicad_sch]
2025-05-18 Started routing for BL
    [horizon.kicad_pcb]
2025-05-18 do some rf routing (and hopefully not break everything)
    [horizon.kicad_pcb, horizon.kicad_sch, sensor.kicad_sch]
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2025-05-19 new usb, move micro sd, redo boost converter (pls find a place on the pcb tomorrow)
    [horizon.kicad_pcb, usb.kicad_sch]
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2025-05-20 flipped sides, changed footprint
    [horizon.kicad_pcb, horizon.kicad_sch, sensor.kicad_sch]
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2025-05-26 wiring i hate this
    [horizon.kicad_pcb]
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2025-06-01 Huge amount of PCB changes
    [horizon.kicad_pcb, sensor.kicad_sch]
2025-06-01 Wired up the IMU's to the MCU
    [horizon.kicad_pcb, sensor.kicad_sch]
2025-06-01 Ummm, more baro routing to the MCU and stuff
    [horizon.kicad_pcb, horizon.kicad_sch, sensor.kicad_sch]
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2025-06-01 Fixed the TBD's parts
    [horizon.kicad_pcb, sensor.kicad_sch]
2025-06-02 save spot not done dont push
    [horizon.kicad_pcb]
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2025-06-03 wiring + layout done
    wiring and layout done
    a lottt of stuff needs their 3v connected or 5v
    [horizon.kicad_pcb, sensor.kicad_sch]
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2025-06-04 for you scooter <3
    [freerouting.dsn, horizon.kicad_pcb, horizon.kicad_sch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]
2025-06-04 Actually fixed too much broken stuff
    [horizon.kicad_pcb]
2025-06-04 We Getting there... 84 errors left
    [horizon.kicad_pcb]
2025-06-04 Bad DRC should be done
    [horizon.kicad_pcb]
2025-06-04 Changes so meddy can work on it now ;)
    [horizon.kicad_pcb]
2025-06-05 bootloader wiring. scooter can u pls finish
    [horizon.kicad_pcb]
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2025-06-05 I def fixed a lot... not sure what though lol
    [horizon.kicad_pcb]
2025-06-05 drc fixes
    [horizon.kicad_pcb]
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2025-06-06 finished most of drc
    [horizon.kicad_pcb]
2025-06-06 fixed stuffs
    [horizon.kicad_pcb]
2025-06-06 Fixing some DRC
    [bom.csv, designators.csv, horizon.kicad_pcb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]
2025-06-06 Fixes some more
    [horizon.kicad_pcb]
2025-06-06 More and more fixes
    [horizon.kicad_pcb]
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2025-06-13 Fixed All the DRC errors I'm pretty sure
    [designators.csv, horizon.kicad_pcb, positions.csv]
2025-06-13 Some random tiding up
    [horizon.kicad_pcb]
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2025-06-15 Major ground pour fix and via stitching
    [horizon.kicad_pcb]
2025-06-15 Switched Bl and GPS to U.FL connectors
    [horizon.kicad_pcb, sensor.kicad_sch]
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2025-06-18 added looks only file
    [horizon.kicad_pcb]
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2025-06-24 started to change to bridging and PCB stiching and stuff fixes
    [horizon.kicad_pcb, usb.kicad_sch]
2025-06-25 Wired the headers for programming 3 MCU'S + some footprint fixes and additions for photos:(
    [horizon.kicad_pcb, sensor.kicad_sch, usb.kicad_sch]
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2025-07-02 Started wiring the teensy bootloader
    [horizon.kicad_sch]
2025-07-02 Finished wiring the teensy bootloader
    [horizon.kicad_sch]
2025-07-03 Too tired to finish .routing... @Meddy can you finish when I'm sleeping? Thanks :)
    [horizon.kicad_pcb]
2025-07-03 still some drc, but teensy routing is done
    [horizon.kicad_pcb]
2025-07-04 i fixed the stuff I could I have no clue what the new drc errors are
    [horizon.kicad_pcb, usb.kicad_sch]
2025-07-04 a few small changes to make cyao happy!
    [horizon.kicad_pcb, horizon.kicad_sch]
2025-07-04 forgot to click b ;)
    [horizon.kicad_pcb]
2025-07-06 there is only like 6 real traces left + power
    [horizon.kicad_pcb]
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2025-07-07 Everything is wired besides for power and a few gnd stuff
    [horizon.kicad_pcb]
2025-07-07 some drc fixes
    [horizon.kicad_pcb]
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2025-07-16 umm, routing stuff (lets make it clean this time for cyao :))
    [horizon.kicad_pcb]
2025-07-18 Meddy, the PCB is ready for you. The proper RF is setup too on the PCB
    [horizon.kicad_pcb, horizon.kicad_sch, sensor.kicad_sch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]
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2025-07-20 schematic fixes (3.3V and stuff) + started pcb
    [gs.kicad_pcb, gs.kicad_sch]
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2025-07-20 I think the PCB is done for the ground station
    [gs.kicad_pcb, gs.kicad_sch]
2025-07-20 forgot D+ and D-... I don't want to wire it :(
    [gs.kicad_pcb]
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2025-08-19 power fixes
    [horizon.kicad_pcb, power.kicad_sch]
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2025-08-22 scooter please wire the stuff thats off the board to the side
    [horizon.kicad_pcb]
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2025-08-28 data lines fix :(
    [horizon.kicad_sch]
2025-08-28 wiring we can finish in lit 1-2 days max
    [horizon.kicad_pcb]
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2025-08-31 added buzzer footprint
    [horizon.kicad_pcb, sensor.kicad_sch]
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2025-09-02 FUCK THIS SHIT EXTRA COMMIT BUT IM DONE
    FUCK I FORGOT LEDS AND LOGO AND SWD PINS
    [horizon.kicad_sch]
2025-09-02 fuck i thought i was done
    :( fml
    [horizon.kicad_pcb]
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2025-09-05 FUCK YES 99.99999% DONE
    @scooterthedev CAN U FINISH WIRING LAST LED?
    + CYAO AND MAX CHECK PLEASE
    [horizon.kicad_pcb]
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2025-09-05 i think ima start pushing for fun commit messages
    [horizon.kicad_sch]
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2025-09-12 there are problems that need to be fixed before being ordered
    [horizon.kicad_pcb]
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2025-09-15 fixed all drc. everything else is bs
    [horizon.kicad_pcb]
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2025-09-16 everything everything :) wait no i still havent added the secondary rotary encoder dont push
    [horizon.kicad_pcb, sensor.kicad_sch]
2025-09-16 a lotta bug fixes in the PCB!
    [bom.csv, designators.csv, horizon.kicad_pcb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]
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2025-09-17 idt theres too much that can be improved in terms of wiring efficiency
    [horizon.kicad_pcb]
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2025-09-17 swap spi lines on tmcu
    [horizon.kicad_sch]
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2025-09-18 swapping swd on nmcu
    [horizon.kicad_sch]
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2025-09-19 bluetooth, gps, gyro reviewed - doing pressure tmrw
    [power.kicad_sch]
2025-09-19 only worked on the schematic, so the PCB is fine. Fixed a few small things- max, the baro looks right too
    [sensor.kicad_sch]
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2025-09-24 someone fix the 30deg cap
    [horizon.kicad_pcb]
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2025-09-26 mistake yay!
    [bom.csv, horizon.kicad_pcb, positions.csv]
2025-10-24 fixed micro sd card direction and prod files
    [horizon.kicad_pcb, horizon.kicad_sch, positions.csv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]
2025-10-26 fixed crystal
    [bom.csv, horizon.kicad_pcb, horizon.kicad_sch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]
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2025-10-26 switched back to 12pF for the 2 caps
    [bom.csv, horizon.kicad_pcb, horizon.kicad_sch]
2025-10-26 micro sd card was too slow. part would have went over :(
    [horizon.kicad_pcb, positions.csv]
